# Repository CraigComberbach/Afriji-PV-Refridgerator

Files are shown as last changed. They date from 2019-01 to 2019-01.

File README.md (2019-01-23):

Afriji PV Refridgerator Inverter
================================

Project Details
---------------

* Authors: Craig Comberbach, Mike Mackay
* Processor: PIC24FJ256GA110
* Version Control: This code uses Semantic Versioning (http://semver.org/). The code is setup to auto handle changes to source files it depends upon as long as the associated *.h file has the *_MAJOR, *_MINOR, and _PATCH definitions updated every time the file version changes.

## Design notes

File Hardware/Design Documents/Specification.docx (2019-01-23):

Afriji Spec

Specifications are in black

Details behind specifications are in blue

1. Electrical Ratings
  a. Outputs
    i. 120VAC at 15A initial 0.5 seconds (1800W)
      1. Compressor startup current
    ii. 120VAC at 1A normal operation (120W)
    iii. User LED indicators
      1. Individual Red, Green, Blue
    iv. Console Interface
      1. Outgoing TX only, 3.3V
      2. Used for data logging and debugging during development
  b. Inputs
    i. Vin between a minimum of 9V to a maximum of 37.8V
      1. 3x car batteries @ 12.6V each
    ii. 6x Generic use temperature inputs
      1. 1x for inside of fridge portion
      2. 3x for inside of freezer portion between water shield and freezer interior
      3. 1x for ambient outside air temperature
      4. 1x for ambient enclosure temperature
  c. Longevity
    i. Must last 2000 hours of operation
      1. Not necessarily continuous
      2. We are relying heavily on bulk capacitance which means electrolytic and longer lifespans are hard to come by given the budget
      3. Running for 1 hour a day gives nearly 5.5 years of operation which is an acceptable lifespan

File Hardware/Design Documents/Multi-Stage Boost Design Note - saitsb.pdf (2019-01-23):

1 INTRODUCTION
Devices based on functional material require high voltage for their regular operation e.g. electrostatically actuated MEMS devices, tunable ferroelectric materials [Ning et al. (2014)] etc. all operate on more than 100V. Availability of higher voltage also allows the MEMS chip designers to save the silicon area. For example in MEMS devices comb drives are used for electrostatic actuation. Force generated by the comb drive is directly proportional to the square of applied voltage. This effect enables the designer to reduce the comb size if higher input voltage is available [Khan at al. (2010)]. Analytically saying if a comb drive is designed to generate a certain amount of force at 100V, the same amount of force can be generated by a 16 times smaller comb drive if 400V are applied at its input. This shows that the availability of high voltage can tremendously reduce the size of electrostatic actuators and can help in packing more functionality in the same silicon area.
Supply voltage of digital ICs is continuously reducing. In most of the applications high voltage devices have to be controlled by digital ICs which are mostly operating on either 5V of power supply or 3.3V of battery. To avoid the use of two different voltage sources in a system (one for the digital part and one for the high voltage I/O part) DC-DC converters are required. A number of DC-DC boost converter ICs are available in the market which can provide tens of volts at their output.

LT3494 (2006) is an IC developed by Linear Technology which can perform 3V - 40V conversion. LT3460 (2007) is another IC developed by the same company and is capable of 2.5V 36V conversion and provides better output current as compared to LT3494. Texas Instruments has also developed an IC [TPS61045 (2009)] for DC-DC conversion. Their IC is capable of 1.8V 28V conversion and has the maximum efficiency of 85%. All previously mentioned ICs require off-chip components and their output voltage is less than 50V.
Past research was mainly focused on increasing the efficiency of low voltage DC-DC converters. For example Kong et al. (2012) have improved the efficiency of a 3.7V-8V boost converter. Nakase et al. (2013) have presented a boost system which is capable of 1.03V-5V conversion. Wang et al. (2013) have also represented a 5V-12V boost converter with improved efficiency.
In the last couple of years, research attention has been diverted towards the development of high voltage converters. Jeon et al. (2013) have developed a single stage boost converter which is capable of 3.3V-80V conversion. Shen et al. (2012) have presented a charge pump design which can generate 120V at its output. Test results of this chip are later published by Hofmann et al. (2012). Output of this circuit is not adjustable and the output current is also limited due to the use of charge pump circuit topology.

## Two stage Boost system capable of 5V to 192V-440V DC-DC conversion

### M.B. Saif & K. Hofmann

Integrated Electronic System Lab, Technische Universität Darmstadt, Darmstadt, Hessen, Germany.

ABSTRACT: Numerous electronic and MEMS devices based on functional materials require an ultra-high electrical field and thus a high electrical voltage for their operation, while only a negligible current is needed whereas ubiquitous and mobile computing applications of these devices only support a low voltage source for energy supply. Which often come in the form of a small form factor battery with a typical voltage of 3.7V - 5V. In such scenarios DC-DC conversion becomes essential. In this work a two stage boost system is presented which can provide 192V to 440V at its output while using a 5V input supply. Output can be adjusted by changing the values of inductors from 10µH to 120µH. Converter has been designed and fabricated in 1um SOI process. In the results it is also demonstrated that the two stage boost circuit requires 45.8% less combined inductance as compared to the single stage design.

In none of the previous approaches ultra-high voltage (400V+) conversions were attempted. The highest achieved output voltage is 120V [Shen et al. (2012)]. In this work a two stage boost circuit is represented which is capable of performing ultra- high voltage conversions. By using the 5V input supply the designed converter can generate 192- 440V at the output. Output voltage is adjusted by the varying the value of external inductors from 10µH to 120µH.
The remainder of the paper is organized as follows. In the next section proposed converter topology is discussed. Section 3 elaborates the modified boost circuit architecture. Chip fabrication is presented in Section 4 and results are discussed in Section 5. At the end paper is concluded in Section 6.
2 PROPOSED CONVERTER TOPOLOGY
In this section the design goals and the proposed design is discussed. Design goals can be summarized in following three points
1) System should be capable of doing 5V - 400+ V conversions.
2) Output of the system should be adjustable to widen the application domain.
3) If external components have to be used, their size should be minimal, so that in future they can be monolithically integrated or packaged together with the chip
For high voltage conversion charge pump circuit topology or the boost circuit topology can be used. Charge pumps have the advantage of no off-chip component but their efficiency is compromised due to high number of required stages and in comparison to boost circuits, charge pumps provide less output current. Due to the before mentioned reasons most of the commercially available ICs like LT3494 (2006), TPS61045 (2009), LT3460 (2007) uses the boost circuit.
The output of the charge pump is fixed and to make it adjustable DAC array has to be used as shown by Ning et al. (2014). In contrast to charge pump the output of the boost circuit can be varied by changing the external inductor. This adjustability is the second design goal of this work.
Owing to above mentioned reasons, boost circuit topology was selected. Boost circuits definitely have the disadvantage of external inductors but its output current and efficiency at high voltage conversions make it a better candidate. In order to fulfill the third design goal, 5V- 400+ V conversions should be done by using minimum external inductance. In the next section an endeavor has been made to minimize the required inductance.

3 BOOST CIRCUIT ARCHITECTURE
In this section initially basic operation of the single stage boost circuit is discussed. Later it is improved by using the discontinuous conduction mode (DCM) and two stage architecture.
Schematic of the boost circuit is shown in Figure
1. Its working can be divided into two phases. In charging phase switching stage is closed and the diode is reversed biased. In this circuit configuration inductor charges until a steady state is achieved. The second spike generation phase starts by the opening of switching stage. Opening of switching stage interrupts the inductor current which results in the generation of a voltage spike whose magnitude can be found by using equation 1.
1

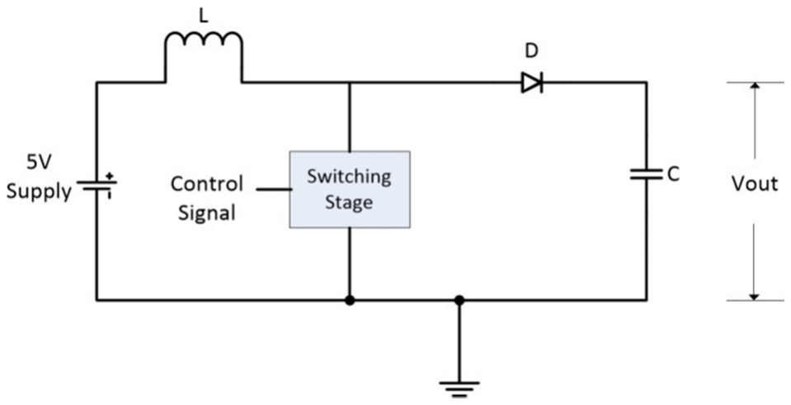
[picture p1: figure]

Figure 1. Single stage Boost circuit
Polarities of the generated voltage spike and the input voltage source add up and momentarily make the diode forward biased which allows the transfer of generated voltage to the capacitor.
From equation (1) it is clear that to increase the generated voltage, either inductance or the rate of change of current has to be changed. Rate of change of inductors current is dependent upon the time required to turn off the high voltage transistors used in the switching stage. Transistors turn off time is the sum of turn off delay, fall time and the reverse recovery time. For the selected technology (xdh10) and transistors the minimum turn-off time is 3.415µs [7].
By using the information of duty cycle and the minimum turn-off time, maximum clock frequency of the boost circuit in continuous conduction mode (CCM) can be determined. In CCM, the duty cycle of the boost circuit can be found by equation (2)
2

For 5V-400V conversion, Vo = 400V and Vs = 5V. By substituting these values in equation (2), the value of required duty cycle is obtained and i.e. D =

98.75%. This implies that turn-off duration for the transistors of switching stage would be only 1.25% time of the clock period. If it is assumed that 1.25% time of the clock period is 3.415 µs (i.e. the minimum turn-off time) then 100% time of the clock period would be
3.415
0.0125 273.2

Maximum operating frequency can be found by taking the inverse of above found time period i.e.

1
273.2

3.66

For a boost circuit the above stated frequency is quite low and if it is used it would result in a very large inductor. Exact value of inductor can be found by using equation (3)
1
2

3

As stated in the introduction the targeted load for this work is the devices which require high voltage but low current. For the sake of calculation, here a load current of 10µA is assumed. At 400V, load current of 10uA results in a load resistance ® of 40

M. By substituting the values of D, R and f in equation
(3) we get the value of minimum required inductor and that is
L 843 mH
In currently available IC technology, fabrication of such a big inductor is not possible. This value should be reduced so that in future at least 3D packaging can be tried. To reduce the inductor size, the boost circuit has to be operated in discontinuous conduction mode (DCM). In DCM the inductor current becomes zero before the start of the next clock cycle. This rapid change in inductor current results in a higher di/dt term. From equation (1) it can be seen that for a fix vL, increase in the rate of change of current results in a reduced value of L. Boost circuit shown in Figure 1 was implemented in cadence ® by using a 1um SOI process (xdh10) from xfab. In post layout simulations it is found that 5V-400V conversion in DCM can be achieved by using a 350µH inductor. To further reduce the inductor size, a multistage approach was analyzed because more inductors connected in series can generate a higher resultant voltage spike. A two stage boost circuit is shown in Figure 2. This concept is also simulated in Cadence ® by using xdh10 technology. The resultant waveform is shown in Figure 4. It can be seen from Figure 4 that with the help of two 120µH external inductor the proposed circuit while operating under discontinuous conduction mode can attain a stable voltage of 435V in just 2ms.
Equivalent circuits of two stage boost when the switches are open and closed are shown in Figure 3. The operation of the circuit can be divided into following two phases.

3.1 Phase 1 (Charging Phase)
When switches are closed, both inductors are in
charging mode. Current | passes
through the inductor L1 and current | passes
through the inductor L2. Maximum value of the charging current is dependent upon the Ron of the switching stages, inductance of the inductor and internal resistance of the inductors.

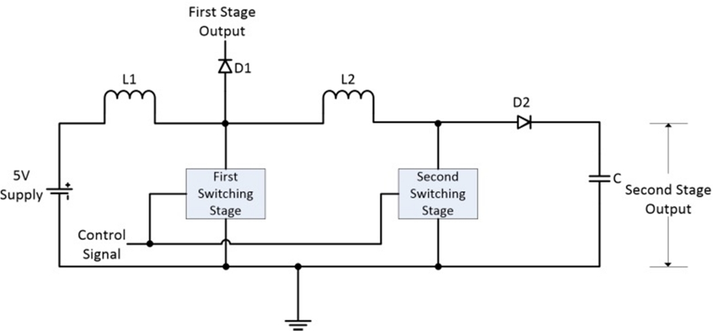
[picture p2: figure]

Figure 2. Two stage Boost Circuit

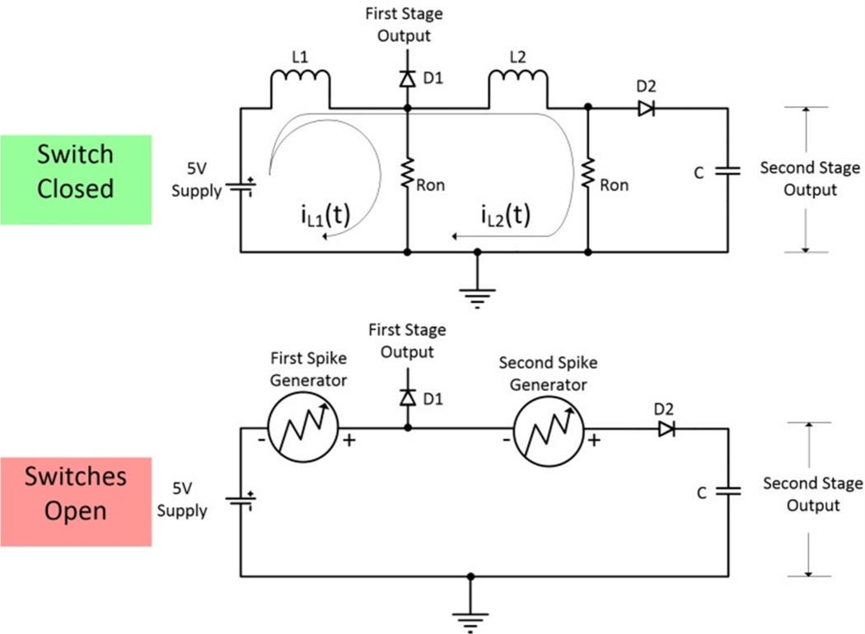
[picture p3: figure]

Figure 3. Equivalent Circuit Topology when switches are close and open

3.2 Phase 2 (Spike Generation)
After the elapse of time DT (D is the duty cycle and T is the time period), switches become open and the normal current flow is interrupted. This interruption in the current flow generates a high voltage spike in both of the inductors and series connection between the inductors adds the generated voltage spikes.

Magnitude of the generated voltage spike can be calculated by using equation (1).
As shown earlier more current passes through L1 in phase 1, which results in a higher voltage spike generated by L1 as compared to L2. Voltage spikes generated by L1 and L2 can be equalized by increasing the inductance of L2.

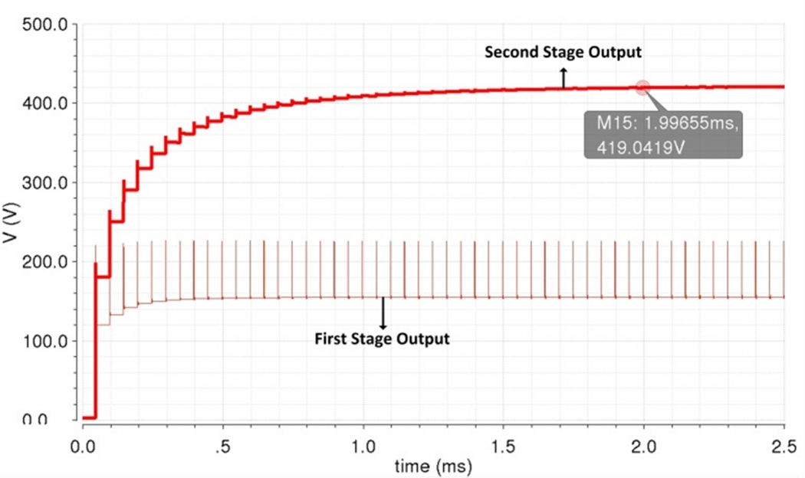
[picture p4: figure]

Figure 4. Transient response of two stage boost converter by using two 120uH inductors
To equalize the voltage spikes L2 L1 and the required value of L2 can be determined by equation (4).

1 4

Inductors of equal inductance can also be used, if the condition formulated in equation (4) is hard to satisfy. In this case the voltages generated by two stages would not be equal.
In the next step designed two stage boost system was simulated in cadence ® with a number of different inductors to ensure the adaptability and stability of the system. It is observed that a number of output voltages can be generated by using different set of inductors.
4 CHIP FABRICATION
To verify the effectiveness of multistage boost architecture a chip has to be designed and fabricated.

As an initial step all the available high voltage IC technologies were analyzed for this specific design and it is found that xdh10 [7] best suits the requirements. Xdh10 is a 1µm SOI process from xfab.
Designed chip includes switching stages, diodes for both stages, and a 265pF capacitor at the output of stage 2. All these components are optimized, to handle the voltage up to 650V. Trenches are placed around the capacitor, diodes and switching stages so that leakage current can be reduced and a problem in one part does not affect the others. Size of the chip is 35 mm² and its picture is shown in Figure 5. Schematic of the chip is shown in Figure 2. Due to the on-chip capacitor for stage 2 its output is automatically low pass filtered. At the output of first stage, voltage spikes are produced (one spike/clock cycle). These spikes can also be converted into a stable voltage by using an external capacitor. Attachment of an external capacitor gives the chip ability to produce two stable output voltages at the same time. Chip output with two 120uH inductor is shown in Figure 6. At the input 5V and the clock signal are supplied externally. Clock current is quite low because it has to only drive the gate terminal of transistors.

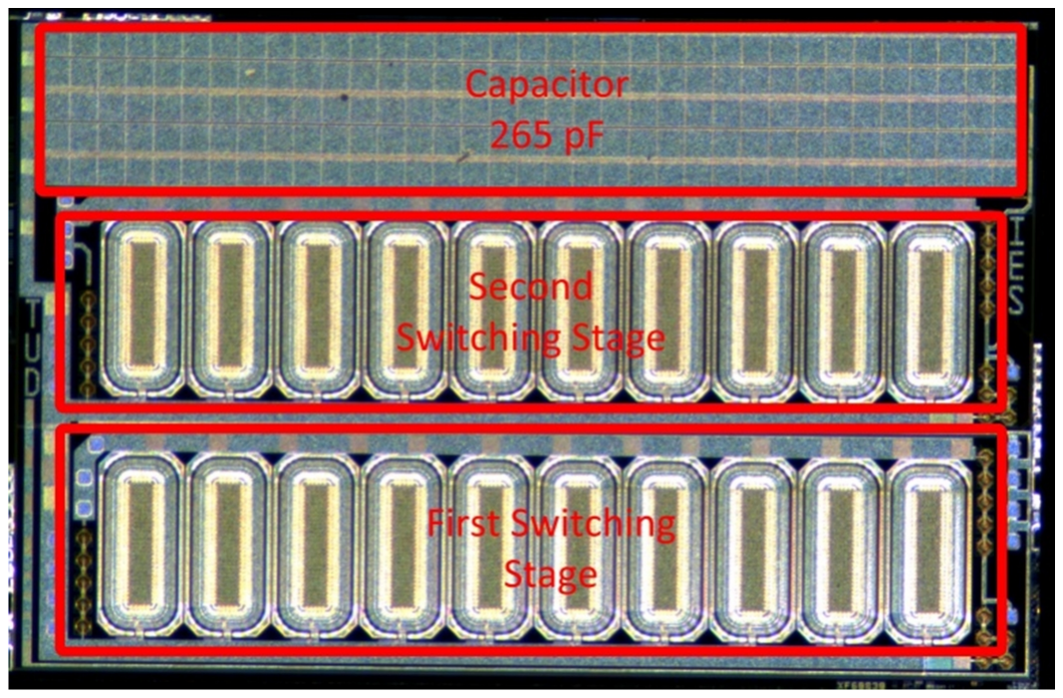
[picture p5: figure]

Figure 5. Picture of fabricated chip

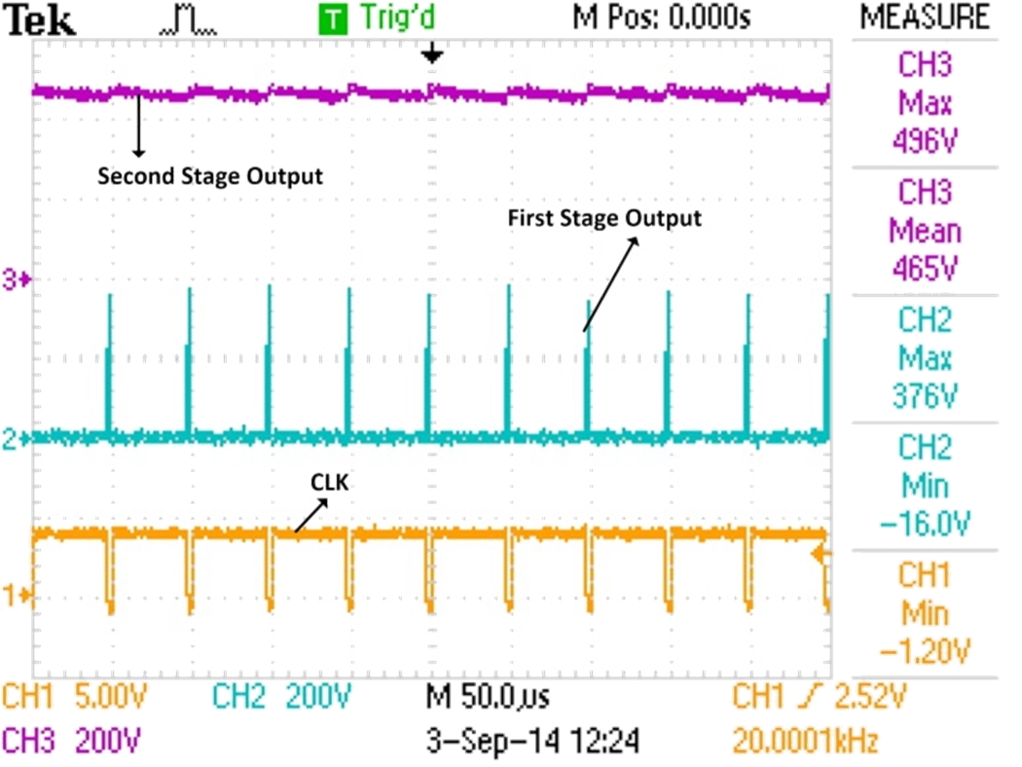
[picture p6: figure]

Figure 6. Chip output when two 120uH inductors are used

5 RESULTS
Figure 6 is showing the output of the designed system when two 120µH inductors are used. As designed, stage 1 is producing the voltage spikes and stage 2 is providing a stable output voltage due to the on-chip capacitor. To verify the adaptability of the output voltage, chip has been tested with a number of external inductors and the results are summarized in Table 1. The test setup is shown in Fig 10.
Figure 7 is showing the Vout vs load current graph. It can be seen that an increase in the load current reduces the output voltage. 100µH and 120µH inductors show better voltage stability whereas worst voltage stability is shown by 10µH inductor. System is designed to provide more than10µA at 400V. It can be seen from zoomed voltage curve of 120µH inductors that actual chip can maintain output voltage higher than 400V while supplying more than 70µA load current.
Operating frequency vs load current graph is shown in Figure 8 and it can be seen there that higher load currents require higher operating frequency. Figure 8 is also showing that larger inductors can operate on lower frequencies whereas smaller inductors require higher operating frequencies. Quantitatively speaking 100µH and 120µH inductors can be operated with less than 100 kHz operating frequency for most of the loading conditions whereas smaller inductors (10µH and 15µH) require higher operating frequency in range of 125 kHz to 200 kHz. Higher frequency increases the losses and reduces the efficiency.
Figure 9 is showing the efficiency vs load current graph. Efficiency increases by increasing the load current but at the cost of output voltage. More than 20% efficiency is shown by 47µH, 100µH and 120µH inductors. Best efficiency (i.e. 34.12%) is shown by 100µH inductor at 2.2mA load current. To compare the efficiency with other high voltage converters, charge pump represented by Shen et al. (2012) is considered here. Their charge pump can provide output voltage of 120V, can supply load current up to 100µA and shows 12% efficiency. The boost system presented in this work when operated with 100µH inductors gives 120V output, while supplying a load current of 1mA-2mA and the efficiency of the system varies from 20-34% (higher load current results in better efficiency). When compared at the output voltage of 120V the boost system presented here surely shows better attributes. At higher voltages (400+V) the efficiency is less due to discontinue conduction mode.
The chip is specifically designed to generate 400+V. Such high voltage can be achieved by using either 100µH or 120µH inductors. Due to this design objective chip shows better stability, better efficiency and better load current when operated with 100µH or 120µH inductors.
Smaller inductors (22µH, 15µH and 10µH) can be used if a voltage less than 260V along with lower output current is required. If output voltage is required in the range of 100-250V with a load current of 1-2mA, then the use of 100µH and 120µH inductors is recommended.
From Figure 9 it can be seen that these lower inductors require higher operating frequencies which results in more switching loses and reduced system efficiency.

Table 1: Output voltage at different inductor values
Sr. No. | Inductor | Vout (V)
1 | 2 x 10µH | 192
2 | 2 x 15µH | 260
3 | 2 x 22µH | 250
4 | 2 x 47µH | 350
5 | 2 x 100µH | 408
6 | 2 x 120µH | 440
Chip temperature has also been analyzed during the working of chip. It is found that normally temperature stays between 40o
| | -50oC and
under any loading condition temperature never exceeds 60oC.

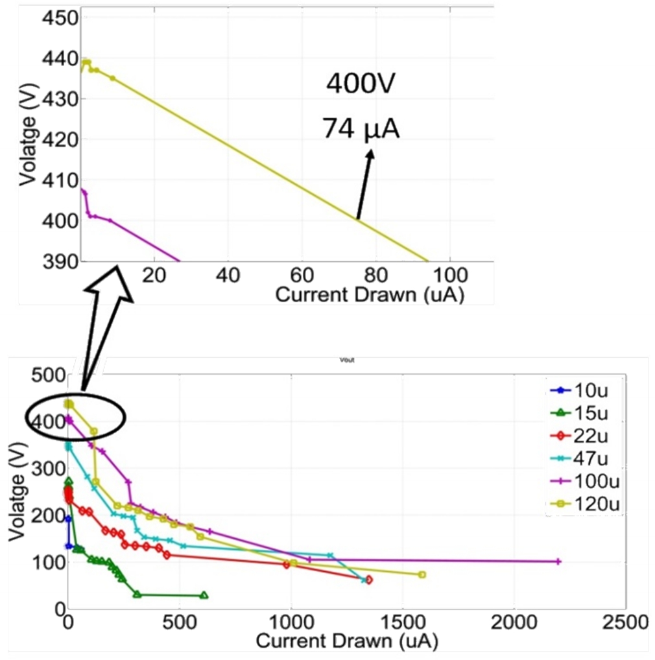
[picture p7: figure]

Figure 7. Output voltage Vs Load current

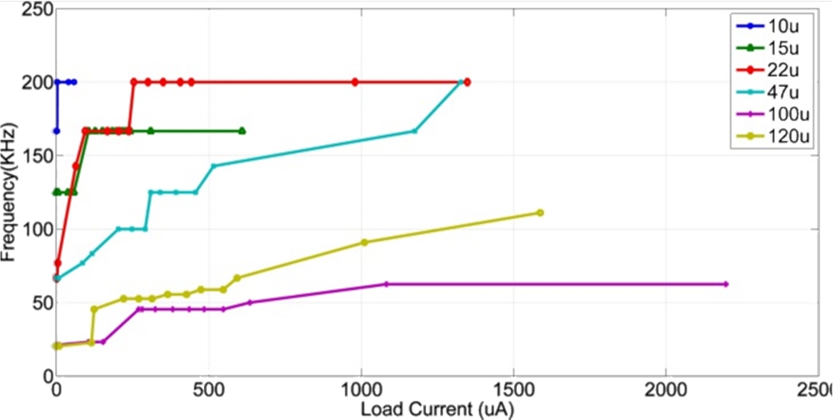
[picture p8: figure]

Figure 8. Frequency vs load current

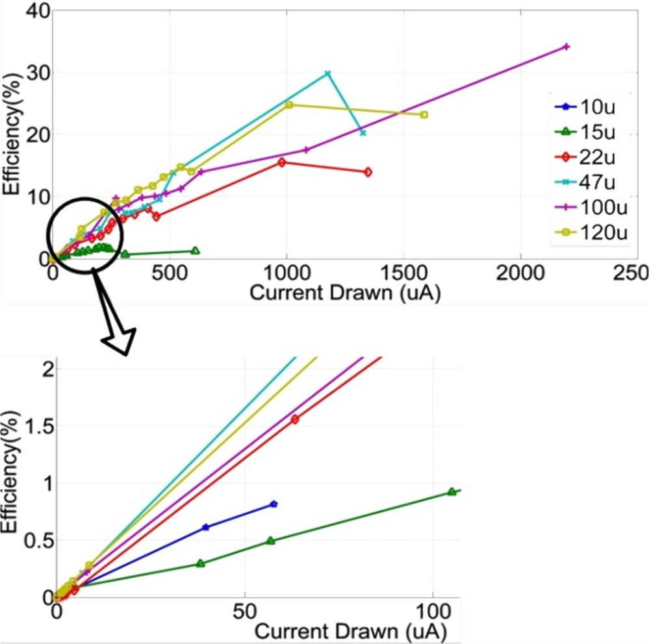
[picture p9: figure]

Figure 9. Efficiency Vs Load current

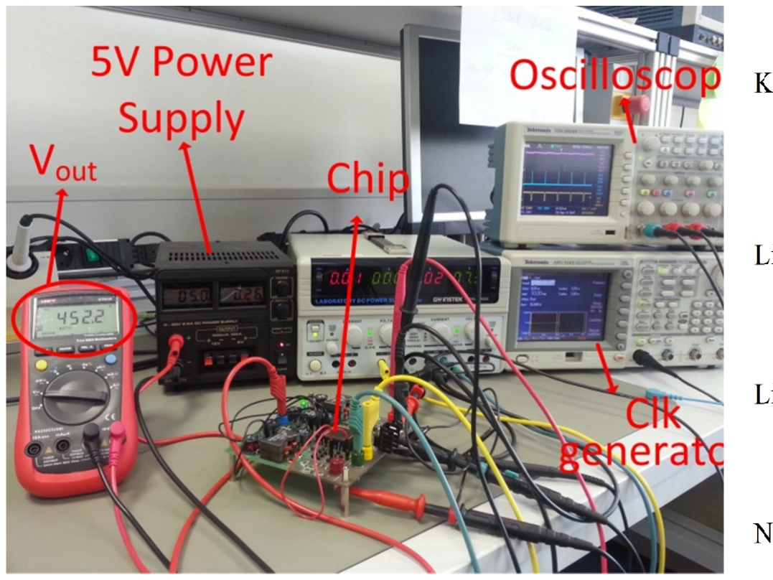
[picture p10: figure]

Figure 10. Test Setup
6 CONCLUSION AND FUTURE WORK
A DC-DC boost converter is presented with a novel two stage architecture. As compared to single stage design, combined inductance (L1 + L2) required by two stage boost converter is 45.8% less. In a single stage design, a single inductor has to bear the full strength of generated voltage spike whereas in two stage architecture the generated voltage spike is divided among the two inductors. This phenomenon reduces the voltage stress on inductors and improves their reliability. If an external capacitor is used with stage 1, two stable output voltages can be attained simultaneously. The presented system can operate with a number of inductors and can produce the output voltages varying from 192V-440V. Inductors can be selected according to the loading conditions.
Output characteristics of the chip are better if larger inductors are used. These inductors also allow the converter to operate on lower frequency, which in turn reduces the switching loses and improves the efficiency.
In future, authors want to further improve the efficiency.

REFERENCES

Hofmann Klaus, Shen Lufei, González- Rodríguez Erick, Maune Holger. 2012. Fully Integrated High Voltage Charge Pump for Energy-efficient Reconfigurable Multi-band RF Transceivers. Telecommunications Energy Conference (INTELEC), IEEE, Sept. 30 - Oct. 4 2012: 1-4.
Jeon Inho, Nam Hyunseok, Lee Heeyoung, Ahn Youngkook, Roh Jeongjin. 2013. An 80-V integrated boost converter for piezoelectric actuators in smartphones. Analog Integrated Circuits and Signal Processing Volume 75, Issue 3, March 2013: 531-537. Khan Fahimullah, Bazaz Shafaat A., Sohail Muhammad. 2010.

Design, implementation and testing of electrostatic SOI MUMPs based microgripper. Journal of Microsystem Technologies, November 2010, Volume 16, Issue 11: 1957- 1965. Kong Tae-Hwang, Hong Sung-Wan, Lee Sungwoo, Im Jong- Pil, Cho Gyu-Hyeong. 2012. A 0.791mm² Fully On-Chip

Controller with Self-Error-Correction for Boost DC-DC Converter Based on Zero-Order Control. Custom Integrated Circuits Conference (CICC), IEEE, 9-12 Sept. 2012: 1-4.
Linear | Technology. | 2007. | LT3460 | Data | sheet,
1.3MHz/650kHz Step-Up DC-DC Converter in SC70, ThinSOT and DFN, 2007, Accessed Dec. 2013, http://cds.linear.com/docs/en/datasheet/34601fb.pdf Linear Technology. 2006. LT3494/LT3494A Data sheet, Micropower Low Noise Boost Converters with Output Disconnect, Nov. 2006, Accessed Dec. 2013, http://cds.linear.com/docs/en/datasheet/3494fb.pdf
Nakase Yasunobu, Hirose Shinichi, Onoda Hiroshi, Ido Yasuhiro, Shimizu Yoshiaki, Oishi Tsukasa, Kumamoto Toshio and Shimizu Toru. 2013. 0.5 V Start-Up 87% Efficiency 0.75 mm² On-Chip Feed-Forward Single-Inductor Dual-Output (SIDO) Boost DC-DC Converter for Battery and Solar Cell Operation Sensor Network Micro- Computer Integration. IEEE Journal of solid-state circuits, vol. 48, no. 8, August 2013:1933-1942. Ning Jing, Shen Lufei, González-Rodríguez Erick, Hofmann

Klaus. 2014. An integrated high voltage digital-to-analog converter for a reconfigurable antenna array, Analog Integrated Circuits and Signal Processing, Volume 80, Issue 3: 407-415.

Shen Lufei, Hofmann Klaus. 2012. Fully Integratable 4-Phase Charge Pump Architecture for High Voltage Applications. 19th International Conference on Mixed Design of Integrated Circuits and Systems, Warsaw (IEEE): 265 268.
Texas Instruments. 2009. TPS61045 Data sheet Rev. B, Digitally Adjustable Boost Converter, Mar. 2009,
Accessed | Dec. | 2013.
http://www.ti.com/lit/ds/symlink/tps61045.pdf
Wang Chen-Yu, Guo Jhih-Sian, Huang Chi-Yuan and Tsai Chien-Hung. 2013. A High Effieciency DC/DC Boost Regulator with Adaptive Off/On-Time Control. International Symposium on VLSI Design, Automation, and Test (VLSI-DAT), IEEE, 22-24 April 2013: 1-4. X-FAB Silicon Foundries, 1.0 Micron Modular 650V Trench Insulated BCD Process Technology (xdh10), Accessed Dec. 2014. http://www.xfab.com/technology/soi/10-um- xdh10/

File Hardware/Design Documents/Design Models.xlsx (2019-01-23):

Don't use this one |  | Thermistor on top
 | Vcc | 3.3
 | Rta (High Temp) | 2000
 | Rtb (Low Temp) | 4500
 | Rb | 2000
 | Rf | 6336.308
 | Vref | 1.425091
Use this one |  | Thermistor on bottom
 | Vcc | 3.3
 | Rt | 2000
 | Rba (Low Temp) | 4500 | 53.5
 | Rbb (High Temp) | 2000 | 76.4
 | Vref Rb | 2000
 | Vref Rt | 1520.171299
 | Rf | 6336.308338
 | Vref | 1.875
188500 | -40
144300 | -35
111300 | -30
86560 | -25
67790 | -20
53460 | -15
42450 | -10
33930 | -5
27280 | 0
22070 | 5
17960 | 10
14700 | 15
12090 | 20
10000 | 25
8312 | 30
6942 | 35
5826 | 40
4911 | 45
4158 | 50
3536 | 55
3019 | 60
2588 | 65
2227 | 70
1924 | 75
1668 | 80
1451 | 85
1267 | 90
1110 | 95
975 | 100
860 | 105
760 | 110
674 | 115
599 | 120
534 | 125

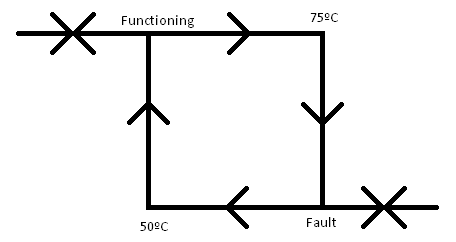
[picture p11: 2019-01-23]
Hardware/Design Documents/Hysterysis.png

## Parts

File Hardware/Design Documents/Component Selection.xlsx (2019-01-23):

Digi-Key Part Number | Description | Quantity Available | Unit Price (CAD) | Capacitance | Voltage - Rated | ESR (Equivalent Series Resistance) | Lifetime @ Temp. | Operating Temperature | Capacitance (mF) | Voltage | F/$
565-2700-ND | CAP ALUM 12000UF 20% 63V SNAP | 926 | 4.15877 | 12000µF | 63V | 21 mOhm @ 120Hz | 2000 Hrs @ 85°C | -40°C ~ 85°C | 12 | 63 | 2.88546854
338-1569-ND | CAP ALUM 10000UF 20% 63V SNAP | 18144 | 3.48091 | 10000µF | 63V | 40 mOhm | 3000 Hrs @ 85°C | -40°C ~ 85°C | 10 | 63 | 2.872811995
338-1570-ND | CAP ALUM 10000UF 20% 63V SNAP | 7934 | 3.60916 | 10000µF | 63V | 40 mOhm | 3000 Hrs @ 85°C | -40°C ~ 85°C | 10 | 63 | 2.770727815
565-4208-ND | CAP ALUM 15000UF 20% 63V SNAP | 194 | 5.42129 | 15000µF | 63V | 14 mOhm @ 120Hz | 2000 Hrs @ 105°C | -40°C ~ 105°C | 15 | 63 | 2.76686914 | 1st Choice input Cap
495-6162-ND | CAP ALUM 6800UF 20% 63V SNAP | 158 | 2.54443 | 6800µF | 63V | - | 2000 Hrs @ 85°C | -40°C ~ 85°C | 6.8 | 63 | 2.672504254
338-3908-ND | CAP ALUM 15000UF 20% 63V SNAP | 663 | 5.62207 | 15000µF | 63V | 24 mOhm @ 120Hz | 3000 Hrs @ 105°C | -40°C ~ 105°C | 15 | 63 | 2.668056428 | 2nd Choice input Cap
338-4413-ND | CAP ALUM 6800UF 20% 63V SNAP | 1000 | 2.56841 | 6800µF | 63V | 59 mOhm @ 120Hz | 3000 Hrs @ 85°C | -40°C ~ 85°C | 6.8 | 63 | 2.647552377
493-6137-ND | CAP ALUM 10000UF 20% 63V SNAP | 1321 | 3.86565 | 10000µF | 63V | - | 3000 Hrs @ 105°C | -40°C ~ 105°C | 10 | 63 | 2.586887069
565-2698-ND | CAP ALUM 10000UF 20% 63V SNAP | 1241 | 3.90229 | 10000µF | 63V | 25 mOhm @ 120Hz | 2000 Hrs @ 85°C | -40°C ~ 85°C | 10 | 63 | 2.562597859
338-1663-ND | CAP ALUM 8200UF 20% 63V SNAP | 685 | 3.2061 | 8200µF | 63V | 49 mOhm | 3000 Hrs @ 85°C | -40°C ~ 85°C | 8.2 | 63 | 2.557624528
495-6154-ND | CAP ALUM 3900UF 20% 63V SNAP | 140 | 1.54939 | 3900µF | 63V | - | 2000 Hrs @ 85°C | -40°C ~ 85°C | 3.9 | 63 | 2.517119641
338-1651-ND | CAP ALUM 6800UF 20% 63V SNAP | 1289 | 2.70158 | 6800µF | 63V | 59 mOhm | 3000 Hrs @ 85°C | -40°C ~ 85°C | 6.8 | 63 | 2.517045581
1572-1070-ND | SNAP MOUNT 85C | 1395 | 4.03786 | 10000µF | 63V | 24.87 mOhm @ 120Hz | 3000 Hrs @ 85°C | -40°C ~ 85°C | 10 | 63 | 2.476559366
495-6152-ND | CAP ALUM 12000UF 20% 63V SNAP | 35 | 4.85451 | 12000µF | 63V | - | 2000 Hrs @ 85°C | -40°C ~ 85°C | 12 | 63 | 2.471928166
565-2699-ND | CAP ALUM 10000UF 20% 63V SNAP | 198 | 4.06717 | 10000µF | 63V | 25 mOhm @ 120Hz | 2000 Hrs @ 85°C | -40°C ~ 85°C | 10 | 63 | 2.458712077
338-1652-ND | CAP ALUM 6800UF 20% 63V SNAP | 223 | 2.81573 | 6800µF | 63V | 59 mOhm | 3000 Hrs @ 85°C | -40°C ~ 85°C | 6.8 | 63 | 2.41500428
493-7179-ND | CAP ALUM 6800UF 20% 63V SNAP | 828 | 2.82137 | 6800µF | 63V | - | 3000 Hrs @ 105°C | -40°C ~ 105°C | 6.8 | 63 | 2.410176616
565-2918-ND | CAP ALUM 10000UF 20% 63V SNAP | 753 | 4.15877 | 10000µF | 63V | 25 mOhm @ 120Hz | 2000 Hrs @ 105°C | -40°C ~ 105°C | 10 | 63 | 2.404557117
495-6169-ND | CAP ALUM 4700UF 20% 63V SNAP | 233 | 1.95998 | 4700µF | 63V | - | 2000 Hrs @ 85°C | -40°C ~ 85°C | 4.7 | 63 | 2.397983653
338-2104-ND | CAP ALUM 22000UF 20% 63V SNAP | 113 | 9.1815 | 22000µF | 63V | - | 3000 Hrs @ 85°C | -40°C ~ 85°C | 22 | 63 | 2.396122638
565-2697-ND | CAP ALUM 8200UF 20% 63V SNAP | 107 | 3.46259 | 8200µF | 63V | 30 mOhm @ 120Hz | 2000 Hrs @ 85°C | -40°C ~ 85°C | 8.2 | 63 | 2.368169492
338-3812-ND | CAP ALUM 18000UF 20% 63V SNAP | 2501 | 7.6117 | 18000µF | 63V | 23 mOhm @ 120Hz | 3000 Hrs @ 85°C | -40°C ~ 85°C | 18 | 63 | 2.364780535
565-2695-ND | CAP ALUM 6800UF 20% 63V SNAP | 683 | 2.87633 | 6800µF | 63V | 37 mOhm @ 120Hz | 2000 Hrs @ 85°C | -40°C ~ 85°C | 6.8 | 63 | 2.364123727
338-2102-ND | CAP ALUM 18000UF 20% 63V SNAP | 560 | 7.68472 | 18000µF | 63V | - | 3000 Hrs @ 85°C | -40°C ~ 85°C | 18 | 63 | 2.342310455
1572-1326-ND | CAP ALUM 10000UF 20% 63V SNAP | 60 | 4.36397 | 10000µF | 63V | 49.74 mOhm @ 120Hz | 2000 Hrs @ 85°C | -40°C ~ 85°C | 10 | 63 | 2.291491463
338-2721-ND | CAP ALUM 12000UF 20% 63V SNAP | 33 | 5.23875 | 12000µF | 63V | - | 3000 Hrs @ 105°C | -40°C ~ 105°C | 12 | 63 | 2.290622763
338-1629-ND | CAP ALUM 4700UF 20% 63V SNAP | 9 | 2.07376 | 4700µF | 63V | 85 mOhm | 3000 Hrs @ 85°C | -40°C ~ 85°C | 4.7 | 63 | 2.266414629
493-1133-ND | CAP ALUM 4700UF 20% 63V RADIAL | 1587 | 2.07984 | 4700µF | 63V | - | 2000 Hrs @ 85°C | -40°C ~ 85°C | 4.7 | 63 | 2.259789215
1189-2901-ND | CAP ALUM 10000UF 20% 63V SNAP | 288 | 4.43157 | 10000µF | 63V | - | 2000 Hrs @ 105°C | -40°C ~ 105°C | 10 | 63 | 2.256536622
493-12479-ND | CAP ALUM 6800UF 20% 63V RADIAL | 183 | 3.05221 | 6800µF | 63V | - | 1000 Hrs @ 105°C | -55°C ~ 105°C | 6.8 | 63 | 2.227893887
565-2696-ND | CAP ALUM 6800UF 20% 63V SNAP | 427 | 3.05954 | 6800µF | 63V | 37 mOhm @ 120Hz | 2000 Hrs @ 85°C | -40°C ~ 85°C | 6.8 | 63 | 2.222556332
493-7281-ND | CAP ALUM 12000UF 20% 63V SNAP | 185 | 5.42074 | 12000µF | 63V | - | 3000 Hrs @ 85°C | -40°C ~ 85°C | 12 | 63 | 2.213719898
338-2719-ND | CAP ALUM 10000UF 63V 20% SNAP | 1006 | 4.56183 | 10000µF | 63V | - | 3000 Hrs @ 105°C | -40°C ~ 105°C | 10 | 63 | 2.192102731
565-2917-ND | CAP ALUM 8200UF 20% 63V SNAP | 825 | 3.75572 | 8200µF | 63V | 30 mOhm @ 120Hz | 2000 Hrs @ 105°C | -40°C ~ 105°C | 8.2 | 63 | 2.183336351
493-7280-ND | CAP ALUM 10000UF 20% 63V SNAP | 1 | 4.59221 | 10000µF | 63V | - | 3000 Hrs @ 85°C | -40°C ~ 85°C | 10 | 63 | 2.177600763
1572-1501-ND | CAP ALUM 4700UF 20% 63V SNAP | 45 | 2.17649 | 4700µF | 63V | 105.82 mOhm @ 120Hz | 2000 Hrs @ 85°C | -40°C ~ 85°C | 4.7 | 63 | 2.1594402
399-6531-ND | CAP ALUM 12000UF 20% 63V SNAP | 334 | 5.56092 | 12000µF | 63V | - | 2000 Hrs @ 85°C | -40°C ~ 85°C | 12 | 63 | 2.157916316
493-7293-ND | CAP ALUM 6800UF 20% 63V SNAP | 160 | 3.17001 | 6800µF | 63V | - | 3000 Hrs @ 85°C | -40°C ~ 85°C | 6.8 | 63 | 2.145103643
493-1130-ND | CAP ALUM 2200UF 20% 63V RADIAL | 1296 | 1.03325 | 2200µF | 63V | - | 2000 Hrs @ 85°C | -40°C ~ 85°C | 2.2 | 63 | 2.129203968
493-7295-ND | CAP ALUM 8200UF 20% 63V SNAP | 66 | 3.88011 | 8200µF | 63V | - | 3000 Hrs @ 85°C | -40°C ~ 85°C | 8.2 | 63 | 2.113342148
565-2691-ND | CAP ALUM 4700UF 20% 63V SNAP | 177 | 2.22596 | 4700µF | 63V | 53 mOhm @ 120Hz | 2000 Hrs @ 85°C | -40°C ~ 85°C | 4.7 | 63 | 2.111448544
493-13920-ND | CAP ALUM 6800UF 20% 80V SNAP | 68 | 3.22442 | 6800µF | 80V | - | 3000 Hrs @ 85°C | -40°C ~ 85°C | 6.8 | 80 | 2.108906408
495-6153-ND | CAP ALUM 2200UF 20% 63V SNAP | 340 | 1.04449 | 2200µF | 63V | - | 2000 Hrs @ 85°C | -40°C ~ 85°C | 2.2 | 63 | 2.106291109
493-7176-ND | CAP ALUM 4700UF 20% 63V SNAP | 651 | 2.24498 | 4700µF | 63V | - | 3000 Hrs @ 105°C | -40°C ~ 105°C | 4.7 | 63 | 2.093559854
565-2693-ND | CAP ALUM 5600UF 20% 63V SNAP | 71 | 2.68256 | 5600µF | 63V | 44 mOhm @ 120Hz | 2000 Hrs @ 85°C | -40°C ~ 85°C | 5.6 | 63 | 2.087558153
493-13922-ND | CAP ALUM 8200UF 20% 80V SNAP | 124 | 3.95725 | 8200µF | 80V | - | 3000 Hrs @ 85°C | -40°C ~ 85°C | 8.2 | 80 | 2.072146061
1572-1081-ND | SNAP MOUNT 85C | 108 | 7.26489 | 15000µF | 63V | 16.58 mOhm @ 120Hz | 3000 Hrs @ 85°C | -40°C ~ 85°C | 15 | 63 | 2.064724999
P5198-ND | CAP ALUM 2200UF 20% 63V RADIAL | 1080 | 1.067 | 2200µF | 63V | - | 2000 Hrs @ 85°C | -40°C ~ 85°C | 2.2 | 63 | 2.06185567
493-7294-ND | CAP ALUM 6800UF 20% 63V SNAP | 194 | 3.30101 | 6800µF | 63V | - | 3000 Hrs @ 85°C | -40°C ~ 85°C | 6.8 | 63 | 2.059975583
565-2689-ND | CAP ALUM 3900UF 20% 63V SNAP | 460 | 1.92156 | 3900µF | 63V | 64 mOhm @ 120Hz | 2000 Hrs @ 85°C | -40°C ~ 85°C | 3.9 | 63 | 2.029600949
493-7292-ND | CAP ALUM 5600UF 20% 63V SNAP | 39 | 2.77666 | 5600µF | 63V | - | 3000 Hrs @ 85°C | -40°C ~ 85°C | 5.6 | 63 | 2.016811565
1189-2867-ND | CAP ALUM 6800UF 20% 63V SNAP | 69 | 3.37429 | 6800µF | 63V | - | 2000 Hrs @ 105°C | -40°C ~ 105°C | 6.8 | 63 | 2.015238761
565-2916-ND | CAP ALUM 6800UF 20% 63V SNAP | 871 | 3.40763 | 6800µF | 63V | 37 mOhm @ 120Hz | 2000 Hrs @ 105°C | -40°C ~ 105°C | 6.8 | 63 | 1.995521814
493-8447-ND | CAP ALUM 5600UF 20% 63V SNAP | 4 | 2.81573 | 5600µF | 63V | - | 3000 Hrs @ 105°C | -40°C ~ 105°C | 5.6 | 63 | 1.988827054
493-7291-ND | CAP ALUM 5600UF 20% 63V SNAP | 1086 | 2.8203 | 5600µF | 63V | - | 3000 Hrs @ 85°C | -40°C ~ 85°C | 5.6 | 63 | 1.985604368
493-12414-ND | CAP ALUM 6800UF 20% 63V RADIAL | 123 | 3.43859 | 6800µF | 63V | - | 2000 Hrs @ 85°C | -40°C ~ 85°C | 6.8 | 63 | 1.977554754
565-2694-ND | CAP ALUM 5600UF 20% 63V SNAP | 153 | 2.83477 | 5600µF | 63V | 44 mOhm @ 120Hz | 2000 Hrs @ 85°C | -40°C ~ 85°C | 5.6 | 63 | 1.975468909
338-2323-ND | CAP ALUM 6800UF 63V 20% SNAP | 1269 | 3.44427 | 6800µF | 63V | - | 3000 Hrs @ 105°C | -40°C ~ 105°C | 6.8 | 63 | 1.974293537
493-7178-ND | CAP ALUM 5600UF 20% 63V SNAP | 118 | 2.85875 | 5600µF | 63V | - | 3000 Hrs @ 105°C | -40°C ~ 105°C | 5.6 | 63 | 1.95889812
338-1458-ND | CAP ALUM 10000UF 20% 63V SNAP | 1330 | 5.14748 | 10000µF | 63V | 40 mOhm | 3000 Hrs @ 105°C | -40°C ~ 105°C | 10 | 63 | 1.942698175
493-13921-ND | CAP ALUM 6800UF 20% 80V SNAP | 182 | 3.51755 | 6800µF | 80V | - | 3000 Hrs @ 85°C | -40°C ~ 85°C | 6.8 | 80 | 1.933163708
1189-2902-ND | CAP ALUM 8200UF 20% 63V SNAP | 58 | 4.24195 | 8200µF | 63V | - | 2000 Hrs @ 105°C | -40°C ~ 105°C | 8.2 | 63 | 1.933073233
338-1987-ND | CAP ALUM 39000UF 20% 80V SNAP | 25 | 20.26258 | 39000µF | 80V | - | 3000 Hrs @ 85°C | -40°C ~ 85°C | 39 | 80 | 1.924730217
493-13918-ND | CAP ALUM 5600UF 20% 80V SNAP | 28 | 2.91297 | 5600µF | 80V | - | 3000 Hrs @ 85°C | -40°C ~ 85°C | 5.6 | 80 | 1.922436551
493-7174-ND | CAP ALUM 3900UF 20% 63V SNAP | 15 | 2.05473 | 3900µF | 63V | - | 3000 Hrs @ 105°C | -40°C ~ 105°C | 3.9 | 63 | 1.898059599
338-2687-ND | CAP ALUM 12000UF 20% 63V SNAP | 1436 | 6.33396 | 12000µF | 63V | 28 mOhm @ 120Hz | 3000 Hrs @ 85°C | -40°C ~ 85°C | 12 | 63 | 1.894549381
493-12411-ND | CAP ALUM 2200UF 20% 63V RADIAL | 168 | 1.16524 | 2200µF | 63V | - | 2000 Hrs @ 85°C | -40°C ~ 85°C | 2.2 | 63 | 1.888023068
493-12413-ND | CAP ALUM 4700UF 20% 63V RADIAL | 250 | 2.51038 | 4700µF | 63V | - | 2000 Hrs @ 85°C | -40°C ~ 85°C | 4.7 | 63 | 1.872226516
493-6162-ND | CAP ALUM 4700UF 20% 80V SNAP | 541 | 2.51133 | 4700µF | 80V | - | 3000 Hrs @ 85°C | -40°C ~ 85°C | 4.7 | 80 | 1.871518279
493-1129-ND | CAP ALUM 1000UF 20% 63V RADIAL | 17792 | 0.53461 | 1000µF | 63V | - | 2000 Hrs @ 85°C | -40°C ~ 85°C | 1 | 63 | 1.870522437
493-7289-ND | CAP ALUM 4700UF 20% 63V SNAP | 8 | 2.51342 | 4700µF | 63V | - | 3000 Hrs @ 85°C | -40°C ~ 85°C | 4.7 | 63 | 1.869962044
338-2024-ND | CAP ALUM 12000UF 20% 63V SNAP | 672 | 6.44348 | 12000µF | 63V | - | 3000 Hrs @ 105°C | -40°C ~ 105°C | 12 | 63 | 1.862347675
1189-2866-ND | CAP ALUM 4700UF 20% 63V SNAP | 180 | 2.52732 | 4700µF | 63V | - | 2000 Hrs @ 105°C | -40°C ~ 105°C | 4.7 | 63 | 1.859677445
338-1589-ND | CAP ALUM 2200UF 20% 63V SNAP | 598 | 1.18379 | 2200µF | 63V | 181 mOhm | 3000 Hrs @ 85°C | -40°C ~ 85°C | 2.2 | 63 | 1.85843773
1572-1055-ND | CAP ALUM 1000UF 20% 63V RADIAL | 1523 | 0.53905 | 1000µF | 63V | 149.2 mOhm @ 120Hz | 2000 Hrs @ 105°C | -40°C ~ 105°C | 1 | 63 | 1.855115481
493-11027-ND | CAP ALUM 2200UF 20% 63V RADIAL | 308 | 1.18774 | 2200µF | 63V | - | 2000 Hrs @ 85°C | -40°C ~ 85°C | 2.2 | 63 | 1.852257228
338-2275-ND | CAP ALUM 8200UF 20% 80V SNAP | 211 | 4.43358 | 8200µF | 80V | 40 mOhm @ 120Hz | 3000 Hrs @ 85°C | -40°C ~ 85°C | 8.2 | 80 | 1.849521154
P5197-ND | CAP ALUM 1000UF 20% 63V RADIAL | 2841 | 0.54307 | 1000µF | 63V | - | 2000 Hrs @ 85°C | -40°C ~ 85°C | 1 | 63 | 1.841383247
338-2025-ND | CAP ALUM 15000UF 20% 63V SNAP | 936 | 8.15931 | 15000µF | 63V | - | 3000 Hrs @ 105°C | -40°C ~ 105°C | 15 | 63 | 1.838390746
493-11033-ND | CAP ALUM 4700UF 20% 63V RADIAL | 240 | 2.56537 | 4700µF | 63V | - | 2000 Hrs @ 85°C | -40°C ~ 85°C | 4.7 | 63 | 1.832094396
493-13919-ND | CAP ALUM 5600UF 20% 80V SNAP | 1010 | 3.05954 | 5600µF | 80V | - | 3000 Hrs @ 85°C | -40°C ~ 85°C | 5.6 | 80 | 1.830340509
493-8446-ND | CAP ALUM 4700UF 20% 63V SNAP | 3047 | 2.56841 | 4700µF | 63V | - | 3000 Hrs @ 105°C | -40°C ~ 105°C | 4.7 | 63 | 1.829925907
565-2912-ND | CAP ALUM 4700UF 20% 63V SNAP | 599 | 2.56841 | 4700µF | 63V | 53 mOhm @ 120Hz | 2000 Hrs @ 105°C | -40°C ~ 105°C | 4.7 | 63 | 1.829925907
338-2568-ND | CAP ALUM 6800UF 20% 63V SNAP | 2173 | 3.71908 | 6800µF | 63V | - | 3000 Hrs @ 105°C | -40°C ~ 105°C | 6.8 | 63 | 1.828409176
338-2101-ND | CAP ALUM 12000UF 20% 63V SNAP | 113 | 6.57126 | 12000µF | 63V | - | 3000 Hrs @ 85°C | -40°C ~ 85°C | 12 | 63 | 1.826133801
565-2688-ND | CAP ALUM 3300UF 20% 63V SNAP | 225 | 1.8112 | 3300µF | 63V | 75 mOhm @ 120Hz | 2000 Hrs @ 85°C | -40°C ~ 85°C | 3.3 | 63 | 1.821996466
565-2914-ND | CAP ALUM 5600UF 20% 63V SNAP | 390 | 3.07786 | 5600µF | 63V | 44 mOhm @ 120Hz | 2000 Hrs @ 105°C | -40°C ~ 105°C | 5.6 | 63 | 1.819445979
493-1363-ND | CAP ALUM 6800UF 20% 63V RADIAL | 820 | 3.73776 | 6800µF | 63V | - | 1000 Hrs @ 105°C | -55°C ~ 105°C | 6.8 | 63 | 1.819271435
338-1986-ND | CAP ALUM 33000UF 20% 80V SNAP | 35 | 18.21856 | 33000µF | 80V | - | 3000 Hrs @ 85°C | -40°C ~ 85°C | 33 | 80 | 1.811339645
338-1542-ND | CAP ALUM 6800UF 20% 63V SNAP | 379 | 3.79236 | 6800µF | 63V | 59 mOhm | 3000 Hrs @ 105°C | -40°C ~ 105°C | 6.8 | 63 | 1.793078716
338-2027-ND | CAP ALUM 18000UF 20% 63V SNAP | 146 | 10.07592 | 18000µF | 63V | - | 3000 Hrs @ 105°C | -40°C ~ 105°C | 18 | 63 | 1.786437368
493-11034-ND | CAP ALUM 6800UF 20% 63V RADIAL | 229 | 3.82369 | 6800µF | 63V | - | 2000 Hrs @ 85°C | -40°C ~ 85°C | 6.8 | 63 | 1.778386846
493-7287-ND | CAP ALUM 3900UF 20% 63V SNAP | 94 | 2.19874 | 3900µF | 63V | - | 3000 Hrs @ 85°C | -40°C ~ 85°C | 3.9 | 63 | 1.773743144
1189-2904-ND | CAP ALUM 6800UF 20% 80V SNAP | 154 | 3.83963 | 6800µF | 80V | - | 3000 Hrs @ 85°C | -40°C ~ 85°C | 6.8 | 80 | 1.771003977
338-1985-ND | CAP ALUM 27000UF 20% 80V SNAP | 252 | 15.33394 | 27000µF | 80V | - | 3000 Hrs @ 85°C | -40°C ~ 85°C | 27 | 80 | 1.760799899
LLS1J472MELB-ND | CAP ALUM 4700UF 20% 63V SNAP | 196 | 2.67571 | 4700µF | 63V | - | 3000 Hrs @ 85°C | -40°C ~ 85°C | 4.7 | 63 | 1.756543123
493-12797-3-ND | CAP ALUM 1000UF 20% 63V RADIAL | 1750 | 0.57024 | 1000µF | 63V | - | 2000 Hrs @ 85°C | -40°C ~ 85°C | 1 | 63 | 1.753647587
493-13917-ND | CAP ALUM 4700UF 20% 80V SNAP | 378 | 2.68256 | 4700µF | 80V | - | 3000 Hrs @ 85°C | -40°C ~ 85°C | 4.7 | 80 | 1.752057736
338-2466-ND | CAP ALUM 6800UF 20% 80V SNAP | 953 | 3.88397 | 6800µF | 80V | 45 mOhm @ 120Hz | 3000 Hrs @ 85°C | -40°C ~ 85°C | 6.8 | 80 | 1.750785923
493-1135-ND | CAP ALUM 6800UF 20% 63V RADIAL | 521 | 3.89551 | 6800µF | 63V | - | 2000 Hrs @ 85°C | -40°C ~ 85°C | 6.8 | 63 | 1.745599421
338-2684-ND | CAP ALUM 10000UF 20% 63V SNAP | 279 | 5.73159 | 10000µF | 63V | 33 mOhm @ 120Hz | 3000 Hrs @ 85°C | -40°C ~ 85°C | 10 | 63 | 1.744716562
493-7173-ND | CAP ALUM 3300UF 20% 63V SNAP | 113 | 1.89407 | 3300µF | 63V | - | 3000 Hrs @ 105°C | -40°C ~ 105°C | 3.3 | 63 | 1.742279852
493-12477-ND | CAP ALUM 3300UF 20% 63V RADIAL | 261 | 1.89919 | 3300µF | 63V | - | 1000 Hrs @ 105°C | -55°C ~ 105°C | 3.3 | 63 | 1.737582864
565-2908-ND | CAP ALUM 3300UF 20% 63V SNAP | 158 | 1.90252 | 3300µF | 63V | 75 mOhm @ 120Hz | 2000 Hrs @ 105°C | -40°C ~ 105°C | 3.3 | 63 | 1.734541555
338-1653-ND | CAP ALUM 6800UF 20% 80V SNAP | 503 | 3.93893 | 6800µF | 80V | 49 mOhm | 3000 Hrs @ 85°C | -40°C ~ 85°C | 6.8 | 80 | 1.726357158
1189-3944-ND | CAP ALUM 5600UF 20% 63V SNAP-IN | 100 | 3.30338 | 5600µF | 63V | - | 2000 Hrs @ 105°C | -40°C ~ 105°C | 5.6 | 63 | 1.695233367
493-13916-ND | CAP ALUM 3900UF 20% 80V SNAP | 100 | 2.30206 | 3900µF | 80V | - | 3000 Hrs @ 85°C | -40°C ~ 85°C | 3.9 | 80 | 1.694134818
565-2913-ND | CAP ALUM 4700UF 20% 63V SNAP | 3430 | 2.77768 | 4700µF | 63V | 53 mOhm @ 120Hz | 2000 Hrs @ 105°C | -40°C ~ 105°C | 4.7 | 63 | 1.69205956
1189-2903-ND | CAP ALUM 4700UF 20% 80V SNAP | 459 | 2.78107 | 4700µF | 80V | - | 3000 Hrs @ 85°C | -40°C ~ 85°C | 4.7 | 80 | 1.689997016
338-2560-ND | CAP ALUM 5600UF 20% 63V SNAP | 2875 | 3.31603 | 5600µF | 63V | - | 3000 Hrs @ 105°C | -40°C ~ 105°C | 5.6 | 63 | 1.688766386
493-7181-ND | CAP ALUM 8200UF 20% 63V SNAP | 132 | 4.86784 | 8200µF | 63V | - | 3000 Hrs @ 105°C | -40°C ~ 105°C | 8.2 | 63 | 1.684525375
493-7286-ND | CAP ALUM 3300UF 20% 63V SNAP | 279 | 1.96264 | 3300µF | 63V | - | 3000 Hrs @ 85°C | -40°C ~ 85°C | 3.3 | 63 | 1.681408715
338-2315-ND | CAP ALUM 4700UF 20% 63V SNAP | 978 | 2.79672 | 4700µF | 63V | - | 3000 Hrs @ 105°C | -40°C ~ 105°C | 4.7 | 63 | 1.680540061
493-12412-ND | CAP ALUM 3300UF 20% 63V RADIAL | 147 | 1.96645 | 3300µF | 63V | - | 2000 Hrs @ 85°C | -40°C ~ 85°C | 3.3 | 63 | 1.678150983
338-1654-ND | CAP ALUM 6800UF 20% 80V SNAP | 1963 | 4.06717 | 6800µF | 80V | 49 mOhm | 3000 Hrs @ 85°C | -40°C ~ 85°C | 6.8 | 80 | 1.671924213
338-2455-ND | CAP ALUM 4700UF 20% 80V SNAP | 1613 | 2.81573 | 4700µF | 80V | 65 mOhm @ 120Hz | 3000 Hrs @ 85°C | -40°C ~ 85°C | 4.7 | 80 | 1.669194134
493-8470-ND | CAP ALUM 6800UF 20% 80V SNAP | 18 | 4.08549 | 6800µF | 80V | - | 3000 Hrs @ 105°C | -40°C ~ 105°C | 6.8 | 80 | 1.664427033
338-2462-ND | CAP ALUM 5600UF 20% 80V SNAP | 2133 | 3.37099 | 5600µF | 80V | 55 mOhm @ 120Hz | 3000 Hrs @ 85°C | -40°C ~ 85°C | 5.6 | 80 | 1.66123305
493-12476-ND | CAP ALUM 2200UF 20% 63V RADIAL | 595 | 1.33177 | 2200µF | 63V | - | 1000 Hrs @ 105°C | -55°C ~ 105°C | 2.2 | 63 | 1.651936896
4653PHBK-ND | CAP ALUM 6800UF 20% 63V SNAP | 38 | 4.14045 | 6800µF | 63V | 59 mOhm | 2000 Hrs @ 105°C | -40°C ~ 105°C | 6.8 | 63 | 1.642333563
493-8693-ND | CAP ALUM 10000UF 20% 63V SNAP | 51 | 6.09411 | 10000µF | 63V | - | 5000 Hrs @ 105°C | -40°C ~ 105°C | 10 | 63 | 1.6409287
338-2456-ND | CAP ALUM 4700UF 20% 80V SNAP | 422 | 2.89465 | 4700µF | 80V | 65 mOhm @ 120Hz | 3000 Hrs @ 85°C | -40°C ~ 85°C | 4.7 | 80 | 1.623685074
338-2108-ND | CAP ALUM 12000UF 20% 80V SNAP | 531 | 7.39266 | 12000µF | 80V | - | 3000 Hrs @ 85°C | -40°C ~ 85°C | 12 | 80 | 1.623231692
493-13915-ND | CAP ALUM 3300UF 20% 80V SNAP | 90 | 2.03571 | 3300µF | 80V | - | 3000 Hrs @ 85°C | -40°C ~ 85°C | 3.3 | 80 | 1.621056044
565-3979-ND | CAP ALUM 1800UF 20% 63V RADIAL | 629 | 1.11075 | 1800µF | 63V | - | 10000 Hrs @ 105°C | -40°C ~ 105°C | 1.8 | 63 | 1.620526671
493-1361-ND | CAP ALUM 3300UF 20% 63V RADIAL | 2942 | 2.04027 | 3300µF | 63V | - | 1000 Hrs @ 105°C | -55°C ~ 105°C | 3.3 | 63 | 1.617432987
338-3709-ND | CAP ALUM 3300UF 20% 63V SNAP | 1278 | 2.05473 | 3300µF | 63V | - | 3000 Hrs @ 105°C | -40°C ~ 105°C | 3.3 | 63 | 1.60605043
493-7285-ND | CAP ALUM 3300UF 20% 63V SNAP | 206 | 2.05758 | 3300µF | 63V | - | 3000 Hrs @ 85°C | -40°C ~ 85°C | 3.3 | 63 | 1.603825854
1189-3955-ND | CAP ALUM 6800UF 20% 80V SNAP-IN | 96 | 4.28024 | 6800µF | 80V | - | 3000 Hrs @ 85°C | -40°C ~ 85°C | 6.8 | 80 | 1.588695961
493-8690-ND | CAP ALUM 6800UF 20% 63V SNAP | 195 | 4.28098 | 6800µF | 63V | - | 5000 Hrs @ 105°C | -40°C ~ 105°C | 6.8 | 63 | 1.588421343
493-16172-ND | CAP ALUM 1000UF 20% 63V RADIAL | 540 | 0.62973 | 1000µF | 63V | - | 1000 Hrs @ 105°C | -55°C ~ 105°C | 1 | 63 | 1.587982151
493-1359-ND | CAP ALUM 1000UF 20% 63V RADIAL | 10550 | 0.63079 | 1000µF | 63V | - | 1000 Hrs @ 105°C | -55°C ~ 105°C | 1 | 63 | 1.585313654
338-1984-ND | CAP ALUM 22000UF 20% 80V SNAP | 68 | 13.88884 | 22000µF | 80V | - | 3000 Hrs @ 85°C | -40°C ~ 85°C | 22 | 80 | 1.584005576
493-12585-3-ND | CAP ALUM 1000UF 20% 63V RADIAL | 500 | 0.63609 | 1000µF | 63V | - | 2000 Hrs @ 85°C | -40°C ~ 85°C | 1 | 63 | 1.572104576
493-10689-ND | CAP ALUM 6800UF 20% 63V RADIAL | 3 | 4.34327 | 6800µF | 63V | - | 2000 Hrs @ 85°C | -40°C ~ 85°C | 6.8 | 63 | 1.565640635
338-2703-ND | CAP ALUM 4700UF 20% 63V SNAP | 6651 | 3.00458 | 4700µF | 63V | 80 mOhm @ 120Hz | 3000 Hrs @ 85°C | -40°C ~ 85°C | 4.7 | 63 | 1.564278535
493-1131-ND | CAP ALUM 3300UF 20% 63V RADIAL | 1027 | 2.11085 | 3300µF | 63V | - | 2000 Hrs @ 85°C | -40°C ~ 85°C | 3.3 | 63 | 1.563351257
493-8692-ND | CAP ALUM 8200UF 20% 63V SNAP | 143 | 5.25043 | 8200µF | 63V | - | 5000 Hrs @ 105°C | -40°C ~ 105°C | 8.2 | 63 | 1.561776845
399-6530-ND | CAP ALUM 6800UF 20% 63V SNAP | 194 | 4.36342 | 6800µF | 63V | - | 2000 Hrs @ 105°C | -40°C ~ 105°C | 6.8 | 63 | 1.558410605
493-7180-ND | CAP ALUM 6800UF 20% 63V SNAP | 200 | 4.36909 | 6800µF | 63V | - | 3000 Hrs @ 105°C | -40°C ~ 105°C | 6.8 | 63 | 1.556388172
493-8443-ND | CAP ALUM 2700UF 20% 63V SNAP | 207 | 1.73623 | 2700µF | 63V | - | 3000 Hrs @ 105°C | -40°C ~ 105°C | 2.7 | 63 | 1.555093507
565-2911-ND | CAP ALUM 3900UF 20% 63V SNAP | 401 | 2.53036 | 3900µF | 63V | 64 mOhm @ 120Hz | 2000 Hrs @ 105°C | -40°C ~ 105°C | 3.9 | 63 | 1.541282663
493-14392-ND | CAP ALUM 10000UF 20% 80V SNAP | 376 | 6.49258 | 10000µF | 80V | - | 3000 Hrs @ 85°C | -40°C ~ 85°C | 10 | 80 | 1.540219759
493-1360-ND | CAP ALUM 2200UF 20% 63V RADIAL | 16116 | 1.42864 | 2200µF | 63V | - | 1000 Hrs @ 105°C | -55°C ~ 105°C | 2.2 | 63 | 1.539926084
338-1630-ND | CAP ALUM 4700UF 20% 80V SNAP | 1295 | 3.05954 | 4700µF | 80V | 71 mOhm | 3000 Hrs @ 85°C | -40°C ~ 85°C | 4.7 | 80 | 1.536178641
338-1610-ND | CAP ALUM 3300UF 20% 80V SNAP | 1198 | 2.16888 | 3300µF | 80V | 101 mOhm | 3000 Hrs @ 85°C | -40°C ~ 85°C | 3.3 | 80 | 1.521522629
493-11030-ND | CAP ALUM 3300UF 20% 63V RADIAL | 16 | 2.16925 | 3300µF | 63V | - | 2000 Hrs @ 85°C | -40°C ~ 85°C | 3.3 | 63 | 1.521263109
338-2450-ND | CAP ALUM 3900UF 20% 80V SNAP | 175 | 2.56841 | 3900µF | 80V | 80 mOhm @ 120Hz | 3000 Hrs @ 85°C | -40°C ~ 85°C | 3.9 | 80 | 1.518449157
493-10711-ND | CAP ALUM 2200UF 20% 63V RADIAL | 163 | 1.45015 | 2200µF | 63V | - | 2000 Hrs @ 85°C | -40°C ~ 85°C | 2.2 | 63 | 1.51708444
493-1960-ND | CAP ALUM 2200UF 20% 63V RADIAL | 24235 | 1.4535 | 2200µF | 63V | - | 8000 Hrs @ 105°C | -55°C ~ 105°C | 2.2 | 63 | 1.513587891
493-11151-ND | CAP ALUM 2200UF 20% 63V RADIAL | 87 | 1.4535 | 2200µF | 63V | - | 3000 Hrs @ 105°C | -55°C ~ 105°C | 2.2 | 63 | 1.513587891
338-1498-ND | CAP ALUM 3300UF 20% 63V SNAP | 615 | 2.18791 | 3300µF | 63V | 121 mOhm | 3000 Hrs @ 105°C | -40°C ~ 105°C | 3.3 | 63 | 1.508288732
493-10696-ND | CAP ALUM 4700UF 20% 63V RADIAL | 128 | 3.13136 | 4700µF | 63V | - | 2000 Hrs @ 85°C | -40°C ~ 85°C | 4.7 | 63 | 1.500945276
338-3710-ND | CAP ALUM 3900UF 20% 63V SNAP | 141 | 2.60646 | 3900µF | 63V | - | 3000 Hrs @ 105°C | -40°C ~ 105°C | 3.9 | 63 | 1.496282314
493-13914-ND | CAP ALUM 3300UF 20% 80V SNAP | 226 | 2.20693 | 3300µF | 80V | - | 3000 Hrs @ 85°C | -40°C ~ 85°C | 3.3 | 80 | 1.495289837
565-2909-ND | CAP ALUM 3300UF 20% 63V SNAP | 348 | 2.20693 | 3300µF | 63V | 75 mOhm @ 120Hz | 2000 Hrs @ 105°C | -40°C ~ 105°C | 3.3 | 63 | 1.495289837
493-14772-ND | CAP ALUM 4700UF 20% 80V SNAP | 191 | 3.16012 | 4700µF | 80V | - | 3000 Hrs @ 85°C | -40°C ~ 85°C | 4.7 | 80 | 1.487285293
338-3844-ND | CAP ALUM 3900UF 20% 80V SNAP | 922 | 2.62548 | 3900µF | 80V | 85 mOhm | 3000 Hrs @ 85°C | -40°C ~ 85°C | 3.9 | 80 | 1.485442662
493-8688-ND | CAP ALUM 5600UF 20% 63V SNAP | 2 | 3.78266 | 5600µF | 63V | - | 5000 Hrs @ 105°C | -40°C ~ 105°C | 5.6 | 63 | 1.480439691
1189-3943-ND | CAP ALUM 3300UF 20% 63V SNAP-IN | 200 | 2.24421 | 3300µF | 63V | - | 2000 Hrs @ 105°C | -40°C ~ 105°C | 3.3 | 63 | 1.470450626
338-2269-ND | CAP ALUM 5600UF 20% 80V SNAP | 557 | 3.81068 | 5600µF | 80V | 55 mOhm @ 120Hz | 3000 Hrs @ 85°C | -40°C ~ 85°C | 5.6 | 80 | 1.46955399
338-2110-ND | CAP ALUM 15000UF 20% 80V SNAP | 147 | 10.24021 | 15000µF | 80V | - | 3000 Hrs @ 85°C | -40°C ~ 85°C | 15 | 80 | 1.46481371
493-7284-ND | CAP ALUM 2700UF 20% 63V SNAP | 131 | 1.84651 | 2700µF | 63V | - | 3000 Hrs @ 85°C | -40°C ~ 85°C | 2.7 | 63 | 1.462217914
399-6060-ND | CAP ALUM 2200UF 20% 63V SNAP | 597 | 1.51052 | 2200µF | 63V | - | 2000 Hrs @ 105°C | -25°C ~ 105°C | 2.2 | 63 | 1.456452083
493-7177-ND | CAP ALUM 4700UF 20% 63V SNAP | 81 | 3.24275 | 4700µF | 63V | - | 3000 Hrs @ 105°C | -40°C ~ 105°C | 4.7 | 63 | 1.449387094
338-2109-ND | CAP ALUM 12000UF 20% 80V SNAP | 50 | 8.28708 | 12000µF | 80V | - | 3000 Hrs @ 85°C | -40°C ~ 85°C | 12 | 80 | 1.448037186
493-15150-ND | CAP ALUM 1000UF 20% 63V RADIAL | 295 | 0.69146 | 1000µF | 63V | - | 2000 Hrs @ 85°C | -40°C ~ 85°C | 1 | 63 | 1.446215255
493-10703-ND | CAP ALUM 3300UF 20% 63V RADIAL | 9 | 2.29122 | 3300µF | 63V | - | 2000 Hrs @ 85°C | -40°C ~ 85°C | 3.3 | 63 | 1.440280724
1189-2870-ND | CAP ALUM 3300UF 20% 80V SNAP | 175 | 2.30053 | 3300µF | 80V | - | 3000 Hrs @ 85°C | -40°C ~ 85°C | 3.3 | 80 | 1.434452061
493-8689-ND | CAP ALUM 5600UF 20% 63V SNAP | 198 | 3.90724 | 5600µF | 63V | - | 5000 Hrs @ 105°C | -40°C ~ 105°C | 5.6 | 63 | 1.43323676
493-7175-ND | CAP ALUM 3900UF 20% 63V SNAP | 123 | 2.7246 | 3900µF | 63V | - | 3000 Hrs @ 105°C | -40°C ~ 105°C | 3.9 | 63 | 1.431402775
493-8444-ND | CAP ALUM 2700UF 20% 63V SNAP | 176 | 1.89407 | 2700µF | 63V | - | 3000 Hrs @ 105°C | -40°C ~ 105°C | 2.7 | 63 | 1.425501697
338-3809-ND | CAP ALUM 3300UF 20% 80V SNAP | 2629 | 2.34011 | 3300µF | 80V | 101 mOhm | 3000 Hrs @ 85°C | -40°C ~ 85°C | 3.3 | 80 | 1.410190119
338-2321-ND | CAP ALUM 5600UF 63V 20% SNAP | 783 | 3.99389 | 5600µF | 63V | - | 3000 Hrs @ 105°C | -40°C ~ 105°C | 5.6 | 63 | 1.402141772
493-6173-ND | CAP ALUM 6800UF 20% 100V SNAP | 596 | 4.85543 | 6800µF | 100V | - | 3000 Hrs @ 85°C | -40°C ~ 85°C | 6.8 | 100 | 1.40049388
338-3819-ND | CAP ALUM 2700UF 20% 63V SNAP | 2194 | 1.93353 | 2700µF | 63V | - | 3000 Hrs @ 105°C | -40°C ~ 105°C | 2.7 | 63 | 1.396409676
338-2039-ND | CAP ALUM 27000UF 20% 80V SNAP | 37 | 19.4455 | 27000µF | 80V | 18 mOhm | 3000 Hrs @ 105°C | -40°C ~ 105°C | 27 | 80 | 1.388496053
493-8683-ND | CAP ALUM 3900UF 20% 63V SNAP | 97 | 2.81112 | 3900µF | 63V | - | 5000 Hrs @ 105°C | -40°C ~ 105°C | 3.9 | 63 | 1.387347392
493-13365-ND | CAP ALUM 10000UF 20% 63V SNAP | 142 | 7.25905 | 10000µF | 63V | - | 1000 Hrs @ 85°C | -40°C ~ 85°C | 10 | 63 | 1.377590732
493-7170-ND | CAP ALUM 2200UF 20% 63V SNAP | 100 | 1.59812 | 2200µF | 63V | - | 3000 Hrs @ 105°C | -40°C ~ 105°C | 2.2 | 63 | 1.376617526
1189-3356-ND | CAP ALUM 3300UF 20% 63V SNAP | 186 | 2.41392 | 3300µF | 63V | - | 2000 Hrs @ 105°C | -40°C ~ 105°C | 3.3 | 63 | 1.367070988
565-2039-ND | CAP ALUM 1800UF 20% 63V RADIAL | 3676 | 1.31796 | 1800µF | 63V | - | 8000 Hrs @ 105°C | -55°C ~ 105°C | 1.8 | 63 | 1.365747064
338-2712-ND | CAP ALUM 8200UF 20% 63V SNAP | 740 | 6.0054 | 8200µF | 63V | 67 mOhm @ 120Hz | 3000 Hrs @ 85°C | -40°C ~ 85°C | 8.2 | 63 | 1.365437773
338-2028-ND | CAP ALUM 18000UF 20% 63V SNAP | 29 | 13.19727 | 18000µF | 63V | 23 mOhm | 3000 Hrs @ 105°C | -40°C ~ 105°C | 18 | 63 | 1.363918447
338-1481-ND | CAP ALUM 2200UF 20% 63V SNAP | 4642 | 1.61785 | 2200µF | 63V | 181 mOhm | 3000 Hrs @ 105°C | -40°C ~ 105°C | 2.2 | 63 | 1.359829403
493-8687-ND | CAP ALUM 4700UF 20% 63V SNAP | 979 | 3.46022 | 4700µF | 63V | - | 5000 Hrs @ 105°C | -40°C ~ 105°C | 4.7 | 63 | 1.358295137
493-1959-ND | CAP ALUM 1500UF 20% 63V RADIAL | 2987 | 1.10685 | 1500µF | 63V | - | 8000 Hrs @ 105°C | -55°C ~ 105°C | 1.5 | 63 | 1.355197181
338-2538-ND | CAP ALUM 2700UF 20% 63V SNAP | 2046 | 1.99766 | 2700µF | 63V | - | 3000 Hrs @ 105°C | -40°C ~ 105°C | 2.7 | 63 | 1.35158135
1189-3853-ND | CAP ALUM 12000UF 20% 63V SNAP | 100 | 8.92632 | 12000µF | 63V | - | 2000 Hrs @ 105°C | -40°C ~ 105°C | 12 | 63 | 1.344338989
565-2718-ND | CAP ALUM 6800UF 20% 100V SNAP | 99 | 5.07447 | 6800µF | 100V | 37 mOhm @ 120Hz | 2000 Hrs @ 85°C | -40°C ~ 85°C | 6.8 | 100 | 1.340041423
565-2906-ND | CAP ALUM 2700UF 20% 63V SNAP | 295 | 2.01667 | 2700µF | 63V | 92 mOhm @ 120Hz | 2000 Hrs @ 105°C | -40°C ~ 105°C | 2.7 | 63 | 1.338840762
1189-3357-ND | CAP ALUM 4700UF 20% 63V SNAP | 147 | 3.51609 | 4700µF | 63V | - | 2000 Hrs @ 105°C | -40°C ~ 105°C | 4.7 | 63 | 1.336712086
338-2106-ND | CAP ALUM 10000UF 20% 80V SNAP | 166 | 7.48393 | 10000µF | 80V | - | 3000 Hrs @ 85°C | -40°C ~ 85°C | 10 | 80 | 1.336196357
1189-3854-ND | CAP ALUM 5600UF 20% 63V SNAP | 100 | 4.19322 | 5600µF | 63V | - | 2000 Hrs @ 105°C | -40°C ~ 105°C | 5.6 | 63 | 1.335489194
565-2904-ND | CAP ALUM 2200UF 20% 63V SNAP | 379 | 1.64744 | 2200µF | 63V | 113 mOhm @ 120Hz | 2000 Hrs @ 105°C | -40°C ~ 105°C | 2.2 | 63 | 1.335405235
493-8684-ND | CAP ALUM 3900UF 20% 63V SNAP | 146 | 2.92983 | 3900µF | 63V | - | 5000 Hrs @ 105°C | -40°C ~ 105°C | 3.9 | 63 | 1.331135254
493-6171-ND | CAP ALUM 4700UF 20% 100V SNAP | 92 | 3.53587 | 4700µF | 100V | - | 3000 Hrs @ 85°C | -40°C ~ 85°C | 4.7 | 100 | 1.329234389
493-1658-ND | CAP ALUM 1500UF 20% 63V RADIAL | 620 | 1.13605 | 1500µF | 63V | - | 10000 Hrs @ 105°C | -40°C ~ 105°C | 1.5 | 63 | 1.320364421
493-8680-ND | CAP ALUM 3300UF 20% 63V SNAP | 51 | 2.50314 | 3300µF | 63V | - | 5000 Hrs @ 105°C | -40°C ~ 105°C | 3.3 | 63 | 1.31834416
1189-1473-ND | CAP ALUM 1000UF 20% 63V RADIAL | 1154 | 0.75932 | 1000µF | 63V | - | 2000 Hrs @ 105°C | -55°C ~ 105°C | 1 | 63 | 1.316967813
399-6075-ND | CAP ALUM 4700UF 20% 80V SNAP | 345 | 3.58387 | 4700µF | 80V | - | 2000 Hrs @ 85°C | -40°C ~ 85°C | 4.7 | 80 | 1.311431497
1189-1505-ND | CAP ALUM 2200UF 20% 63V RADIAL | 9792 | 1.6798 | 2200µF | 63V | - | 10000 Hrs @ 105°C | -40°C ~ 105°C | 2.2 | 63 | 1.309679724
493-7312-ND | CAP ALUM 5600UF 20% 100V SNAP | 36 | 4.30534 | 5600µF | 100V | - | 3000 Hrs @ 85°C | -40°C ~ 85°C | 5.6 | 100 | 1.300710281
338-2031-ND | CAP ALUM 8200UF 20% 80V SNAP | 1 | 6.31571 | 8200µF | 80V | - | 3000 Hrs @ 105°C | -40°C ~ 105°C | 8.2 | 80 | 1.298349671
338-2107-ND | CAP ALUM 10000UF 20% 80V SNAP | 93 | 7.73948 | 10000µF | 80V | - | 3000 Hrs @ 85°C | -40°C ~ 85°C | 10 | 80 | 1.29207647
LLS1J222MELA-ND | CAP ALUM 2200UF 20% 63V SNAP | 5965 | 1.70348 | 2200µF | 63V | - | 3000 Hrs @ 85°C | -40°C ~ 85°C | 2.2 | 63 | 1.291473924
493-7172-ND | CAP ALUM 3300UF 20% 63V SNAP | 511 | 2.56194 | 3300µF | 63V | - | 3000 Hrs @ 105°C | -40°C ~ 105°C | 3.3 | 63 | 1.288086372
338-1590-ND | CAP ALUM 2200UF 20% 80V SNAP | 354 | 1.7165 | 2200µF | 80V | 151 mOhm | 3000 Hrs @ 85°C | -40°C ~ 85°C | 2.2 | 80 | 1.281677833
493-8681-ND | CAP ALUM 3300UF 20% 63V SNAP | 3 | 2.58496 | 3300µF | 63V | - | 5000 Hrs @ 105°C | -40°C ~ 105°C | 3.3 | 63 | 1.276615499
493-7283-ND | CAP ALUM 2200UF 20% 63V SNAP | 74 | 1.72933 | 2200µF | 63V | - | 3000 Hrs @ 85°C | -40°C ~ 85°C | 2.2 | 63 | 1.27216899
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

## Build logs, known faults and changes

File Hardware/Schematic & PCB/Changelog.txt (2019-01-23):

0.1.0   Craig Comberbach    2017
Initial version
Designed to be milled out

0.1.1   Craig Comberbach    2017
Modernized for use with board house standards

0.1.2   Craig Comberbach    2017
Fixed the Drain/Source reversal on Input/Output H-Bridges
Fixed the +/- inputs on Current Sense amplifer
Fixed the TQFP-64 breakout board header
Swapped Current Sense amplifier sub-components to aide in routing
Add a 100nF capacitor to the MCLR line
Layed the board out to be laser milled
Removed unnecesary safety logic
Removed Debug RX line
Increased Isense resistors to 3mR (Input) and 33mR (Output)
Replaced battery headers with battery holders
Added a DPST switch to disconnect both power sources if needed
Added Bypass cap for Current Sense amplifier
H-Bridge Control Lines A_IN and B_IN swapped micro pins
H-Bridge Control Lines C_IN and D_IN moved micro pins
Switched Grounds 1, 2, 3, 4, and 5 moved micro pins
Vsense (-T1.P) and Vsense (+Vsolar) swapped micro pins

0.1.3   Craig Comberbach    2017-07-09
Doubled up H-Bridge FETs to improve efficiency and decrease thermal load on H-Bridge FETs
H-Bridge drivers now control one side instead of kitty corner
 -Reduces inductance/ringing on control lines
H-Bridge drivers now have two signal lines instead of one
Each bridge has four control lines now instead of just two
Removed ultimately ineffective but expensive 1uF 250V ceramic capacitors from the H-Bridges
Added by-pass caps to all analog inputs
H-Bridge Drivers now have 44uF (2x 22uF) bootstrap capacitors
Added a 5V buck SMPS to convert incoming voltage to provide a conditioned input for the 3.3V linear and 15V boost SMPS
Added a 15V boost SMPS to convert 5VDC into the voltage required to power the H-Bridge drivers
Fixed HVGND so that it references the rest of the circuit correctly
Removed the DC- voltage rail sensor as it became circuit ground
Added a 6th Temperature sensor as there was a free analog pin

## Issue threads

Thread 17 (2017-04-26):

ADC buffers consistently filling out of order

CraigComberbach, 2017-04-26:
The buffers are not filling sequentially as expected. I have added an extra tab on the ones that I have identified to be matched correctly (even if out of order).

Why are they out of order?
Are the ones without an extra tab aligned correctly?
What was overlooked? I've never experienced this issue before, and I have done lots of ADC work.

Closed 2019-01-23.

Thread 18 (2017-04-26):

ADC channels can be triggered independently

CraigComberbach, 2017-04-26:
Currently triggering a scan causes all of the channels to be read. This works great if we have a single stage inverter and we are sampling at the peaks. The only time this is not optimal is when you have two inverters running at different frequencies or phase shifted such that the code is being called on the peak of one, but not on the other. The code currently assumes everything is at the peak and is processing the new values accordingly.

This obviously leads to some rather confusing readings as the measurement is not taken at a peak, but is system variables are calculated as if it was.

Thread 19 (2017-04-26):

Proper voltage control

CraigComberbach, 2017-04-26:
Currently the code does a simple step and hold to control the output voltage. The reaction time can be abysmal when given a step function. For example, on startup, tracking to 40VDC at 20Hz can take as long as a second. This timing can be sped up by preloading expected starting values, and increasing the slew rate limiting on the feedback voltage. These can lead to accidental over-voltage and instability in output voltage.

Ideally we would lock on much quicker using Mikes formulaes.

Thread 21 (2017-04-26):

Thermistor table is currently a place holder

CraigComberbach, 2017-04-26:
The table is a place holder counting from 0 to 1023 (entire range of ADC). The real temperature values for each step have not been precalculated.

The future table should have a minimum of 1 decimal place of accuracy and be shifted so that it returns a number that is easy to do integer arithmetic on. ie 5.2ºC would be entered as the number 52.

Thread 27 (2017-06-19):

Address error when target frequency is 15Hz

CraigComberbach, 2017-06-19:
14, 16, and 17Hz specifically work (the rest also appears to work), only 15Hz causes an address error causing the code to enter one of the traps.

I haven't found a solution to it, but I did put a kludge into the pot reading mechanism that skips over that value if detected.

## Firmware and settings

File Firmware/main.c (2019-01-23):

/**************************************************************************************************
Target Hardware:		PIC24FJ256GA106
Code assumptions:		
Purpose:				Firmware for Afriji Solar DC to AC appliance power supply device
Notes:					

Version History:
v0.0.A	2017-03-12      Craig Comberbach, Michael MacKay
Compiler: XC16 v1.26	IDE: MPLABx 3.30	Tool: ICD3	Computer: Intel Core2 Quad CPU 2.40 GHz, 5 GB RAM, Windows 10 64 bit Home
 Revision History:
 * v0.0.A   -   Initial prototype firmware
**************************************************************************************************/
/*************    Header Files    ***************/
#include "Config.h"
#include "Scheduler.h"
#include "A2D.h"
#include "Inverter.h"
#include "Pins.h"
#include "Debug.h"

/************* Library Definition ***************/
/************* Semantic Versioning***************/
#if MAJOR_FIRMWARE_VERSION != 0
    #error "Firmware has had a change that loses some previously supported functionality"
#elif MINOR_FIRMWARE_VERSION != 1
    #error "Firmware has new features that this code may benefit from"
#elif PATCH_FIRMWARE_VERSION != 0
	#error "Firmware has had a bug fix, you should check to see that we weren't relying on a bug for functionality"
#endif
/*************Library Dependencies***************/
/************Arbitrary Functionality*************/
/*************   Magic  Numbers   ***************/
/*************    Enumeration     ***************/
/***********  Structure Definitions  ************/
/***********State Machine Definitions************/
/*************  Global Variables  ***************/
/*************Interrupt Prototypes***************/
/*************Function  Prototypes***************/
/************* Device Definitions ***************/
/************* Module Definitions ***************/
/************* Other  Definitions ***************/

_CONFIG1( JTAGEN_OFF & GCP_OFF & GWRP_OFF & BKBUG_OFF & COE_OFF & ICS_PGx3 & FWDTEN_ON & WINDIS_OFF & FWPSA_PR32 & WDTPS_PS1024 )
_CONFIG2( IESO_OFF & FNOSC_FRCPLL & FCKSM_CSDCMD & OSCIOFNC_ON & IOL1WAY_ON & POSCMOD_NONE )
_CONFIG3( WPDIS_WPDIS )

int main(void)
{
	ClrWdt();
	Configure_For_Afriji();

	//Scheduled Tasks
	Initialize_Scheduler(500/*uS*/);
	Schedule_Task(STARTUP_TASK,			&Heart_Beat_Task,	1000/*uS Delay*/,		50000/*uS Period*/,		20/*Repetitions*/);
	Schedule_Task(HEART_BEAT_TASK,		&Heart_Beat_Task,	1000000/*uS Delay*/,	500000/*uS Period*/,	PERMANENT_TASK);
	Schedule_Task(INVERTER_TASK,		&Inverter_Routine,	1000000/*uS Delay*/,	500/*uS Period*/,		PERMANENT_TASK);
	Schedule_Task(A2D_TASK,				&A2D_Routine,		16667/*uS Delay*/,		16667/*uS Period*/,		PERMANENT_TASK);//No longer than once ever 8mS will allow the result to be captured in time to be used with a 60Hz waveform
	Schedule_Task(FREQUENCY_RAMP_TASK,	&Frequency_Ramp,	2500000/*uS Delay*/,	500000/*uS Period*/,	40/*Repetitions*/);
	Schedule_Task(TERMINAL_TASK,		&Debug_Routine,		200000/*uS Delay*/,		100000/*uS Period*/,	1);

	while(1)
	{
		ClrWdt();
		while(Waiting_To_Run_Tasks())
		{
			ClrWdt();
			Task_Master();
			ClrWdt();
		}
		ClrWdt();
	}

	return 1;
}

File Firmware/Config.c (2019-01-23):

/**************************************************************************************************
Authours:				Craig Comberbach
Target Hardware:		PIC
Chip resources used:
Code assumptions:
Purpose:

Version History:
v0.0.0	2013-07-11  Craig Comberbach
	Compiler: C30 v3.31		IDE: MPLABx 1.80	Tool: RealICE	Computer: Intel Xeon CPU 3.07 GHz, 6 GB RAM, Windows 7 64 bit Professional SP1
	First version
**************************************************************************************************/
/*************    Header Files    ***************/
#include "Config.h"
#include "Pins.h"
#include "A2D.h"
#include "Scheduler.h"
#include "Analogs.h"
#include "Inverter.h"
#include "Debug.h"

/*************Semantic  Versioning***************/
/*************Library Dependencies***************/
#ifndef PINS_LIBRARY
	#error "You need to include the Pins library for this code to compile"
#endif

#ifndef A2D_LIBRARY
	#error "You need to include the A2D library for this code to compile"
#endif

#ifndef INVERTER_LIBRARY
	#error "You need to include the Inverter library for this code to compile"
#endif

#ifndef SCHEDULER_LIBRARY
	#error "You need to include the Scheduler library for this code to compile"
#endif

/************Arbitrary Functionality*************/
/*************   Magic  Numbers   ***************/
/***********State Machine Definitions*************/
/*************  Global Variables  ***************/
volatile int dummy;
const char compiledOnDate[] = __DATE__;
const char compiledAtTime[] = __TIME__;

/*************Function  Prototypes***************/
void __attribute__((interrupt, auto_psv)) _OscillatorFail(void);
void __attribute__((interrupt, auto_psv)) _AddressError(void);
void __attribute__((interrupt, auto_psv)) _StackError(void);
void __attribute__((interrupt, auto_psv)) _MathError(void);
void __attribute__((interrupt, auto_psv)) _DefaultInterrupt(void);

/************* Device Definitions ***************/
/************* Module Definitions ***************/
/************* Other  Definitions ***************/

void Configure_For_Afriji(void)
{
	/*************       Clock        ***************/
	CLKDIVbits.RCDIV	= 0;
	OSCTUNbits.TUN		= 0b000001; //+0.77%

	/*************        Pins        ***************/
	//PORTB
	Pin_Definition(PIN_RB0_TRANSFORMER_PRIMARY_MINUS,	Rx0, &TRISB, &ODCB, &LATB, &PORTB);	//RB0
	Pin_Definition(PIN_RB1_TRANSFORMER_PRIMARY_PLUS,	Rx1, &TRISB, &ODCB, &LATB, &PORTB);	//RB1
	Pin_Definition(PIN_RB2_VSOLAR_PLUS,					Rx2, &TRISB, &ODCB, &LATB, &PORTB);	//RB2
	Pin_Definition(PIN_RB3_TEMP2,						Rx3, &TRISB, &ODCB, &LATB, &PORTB);	//RB3
//	Pin_Definition(PIN_RB4_PGD,							Rx4, &TRISB, &ODCB, &LATB, &PORTB);	//RB4
//	Pin_Definition(PIN_RB5_PGC,							Rx5, &TRISB, &ODCB, &LATB, &PORTB);	//RB5
	Pin_Definition(PIN_RB6_TEMP1,						Rx6, &TRISB, &ODCB, &LATB, &PORTB);	//RB6
	Pin_Definition(PIN_RB7_TEMP3,						Rx7, &TRISB, &ODCB, &LATB, &PORTB);	//RB7
	Pin_Definition(PIN_RB8_TEMP4,						Rx8, &TRISB, &ODCB, &LATB, &PORTB);	//RB8
	Pin_Definition(PIN_RB9_INPUT_CURRENT,				Rx9, &TRISB, &ODCB, &LATB, &PORTB);	//RB9
	Pin_Definition(PIN_RB10_OUTPUT_CURRENT,				Rx10, &TRISB, &ODCB, &LATB, &PORTB);//RB10
	Pin_Definition(PIN_RB11_TEMP5,						Rx11, &TRISB, &ODCB, &LATB, &PORTB);//RB11
	Pin_Definition(PIN_RB12_VDC_BUS_PLUS,				Rx12, &TRISB, &ODCB, &LATB, &PORTB);//RB12
	Pin_Definition(PIN_RB13_TRANSFORMER_SECONDARY_PLUS,	Rx13, &TRISB, &ODCB, &LATB, &PORTB);//RB13
	Pin_Definition(PIN_RB14_VOUT_PLUS,					Rx14, &TRISB, &ODCB, &LATB, &PORTB);//RB14
	Pin_Definition(PIN_RB15_VOUT_MINUS,					Rx15, &TRISB, &ODCB, &LATB, &PORTB);//RB15
	//PORTC
	Pin_Definition(PIN_RC12,							Rx12, &TRISC, &ODCC, &LATC, &PORTC);//RC12
	Pin_Definition(PIN_RC13,							Rx13, &TRISC, &ODCC, &LATC, &PORTC);//RC13
	Pin_Definition(PIN_RC14,							Rx14, &TRISC, &ODCC, &LATC, &PORTC);//RC14
	Pin_Definition(PIN_RC15,							Rx15, &TRISC, &ODCC, &LATC, &PORTC);//RC15
	//PORTD
	Pin_Definition(PIN_RD0_HOB_HiA,						Rx0, &TRISD, &ODCD, &LATD, &PORTD);	//RD0
	Pin_Definition(PIN_RD1_TERMINAL_TX,					Rx1, &TRISD, &ODCD, &LATD, &PORTD);	//RD1
	Pin_Definition(PIN_RD2,								Rx2, &TRISD, &ODCD, &LATD, &PORTD);	//RD2
	Pin_Definition(PIN_RD3,								Rx3, &TRISD, &ODCD, &LATD, &PORTD);	//RD3
	Pin_Definition(PIN_RD4_LOB_HiA,						Rx4, &TRISD, &ODCD, &LATD, &PORTD);	//RD4
	Pin_Definition(PIN_RD5_LOA_HiA,						Rx5, &TRISD, &ODCD, &LATD, &PORTD);	//RD5
	Pin_Definition(PIN_RD6,								Rx6, &TRISD, &ODCD, &LATD, &PORTD);	//RD6
	Pin_Definition(PIN_RD7,								Rx7, &TRISD, &ODCD, &LATD, &PORTD);	//RD7
	Pin_Definition(PIN_RD8_HOA_HiA,						Rx8, &TRISD, &ODCD, &LATD, &PORTD);	//RD8
	Pin_Definition(PIN_RD9_GREEN_LED,					Rx9, &TRISD, &ODCD, &LATD, &PORTD);	//RD9
	Pin_Definition(PIN_RD10_RED_LED,					Rx10, &TRISD, &ODCD, &LATD, &PORTD);//RD10
	Pin_Definition(PIN_RD11_BLUE_LED,					Rx11, &TRISD, &ODCD, &LATD, &PORTD);//RD11
	//PORTE
	Pin_Definition(PIN_RE0,								Rx0, &TRISE, &ODCE, &LATE, &PORTE);	//RE0
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

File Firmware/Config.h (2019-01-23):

#ifndef CONFIG_H
#define	CONFIG_H

//Hardware specific include file
#include <p24FJ256GA106.h>
#include <stdint.h>

//System Variables
#define HiI_INVERTER_ENABLED
#define HiV_INVERTER_ENABLED
//#define	TERMINAL_WINDOW_DEBUG_ENABLED

//Clock Frequency
#define FOSC_Hz			32000000			//32MHz
#define TOSC_ps			31250				//32MHz
#define FOSC_kHz		FOSC_Hz/1000		//32MHz
#define TOSC_ns			TOSC_ps/1000		//32MHz
#define FOSC_MHz		FOSC_kHz/1000		//32MHz
#define TOSC_us			TOSC_ns/1000		//32MHz
#define FCY_Hz			FOSC_Hz/2			//16MHz
#define TCY_ps			TOSC_ps*2			//16MHz
#define FCY_kHz			FCY_Hz/1000			//16MHz
#define TCY_ns			TCY_ps/1000			//16MHz
#define FCY_MHz			FCY_kHz/1000		//16MHz
#define TCY_us			TCY_ns/1000			//16MHz

//Compiled information
extern const char compiledOnDate[];
extern const char compiledAtTime[];
#define MAJOR_FIRMWARE_VERSION	0
#define MINOR_FIRMWARE_VERSION	1
#define PATCH_FIRMWARE_VERSION	0

enum SCHEDULER_DEFINITIONS
{
	STARTUP_TASK,
	HEART_BEAT_TASK,
	INVERTER_TASK,
	A2D_TASK,
	FREQUENCY_RAMP_TASK,
	TERMINAL_TASK,
	NUMBER_OF_SCHEDULED_TASKS
};

enum INVERTERS_SUPPORTED
{
	#ifdef HiI_INVERTER_ENABLED
	HIGH_CURRENT_INVERTER,
	#endif
	#ifdef HiV_INVERTER_ENABLED
	HIGH_VOLTAGE_INVERTER,
	#endif
	NUMBER_OF_INVERTERS_SUPPORTED
};

//Pins
enum PIN_DEFINITIONS
{
	//PORTB
	PIN_RB0_TRANSFORMER_PRIMARY_MINUS,		//RB0
	PIN_RB1_TRANSFORMER_PRIMARY_PLUS,		//RB1
	PIN_RB2_VSOLAR_PLUS,					//RB2
	PIN_RB3_TEMP2,							//RB3
	PIN_RB4_PGD,							//RB4 - PGD
	PIN_RB5_PGC,							//RB5 - PGC
	PIN_RB6_TEMP1,							//RB6
	PIN_RB7_TEMP3,							//RB7
	PIN_RB8_TEMP4,							//RB8
	PIN_RB9_INPUT_CURRENT,					//RB9
	PIN_RB10_OUTPUT_CURRENT,				//RB10
	PIN_RB11_TEMP5,							//RB11
	PIN_RB12_VDC_BUS_PLUS,					//RB12
	PIN_RB13_TRANSFORMER_SECONDARY_PLUS,	//RB13
	PIN_RB14_VOUT_PLUS,						//RB14
	PIN_RB15_VOUT_MINUS,					//RB15
	//PORTC
	PIN_RC12,								//RC12 - Unused
	PIN_RC13,								//RC13 - Unused
	PIN_RC14,								//RC14 - Unused
	PIN_RC15,								//RC15 - Unused
	//PORTD
	PIN_RD0_HOB_HiA,						//RD0
	PIN_RD1_TERMINAL_TX,					//RD1
	PIN_RD2,								//RD2 - Unused
	PIN_RD3,								//RD3 - Unused
	PIN_RD4_LOB_HiA,						//RD4
	PIN_RD5_LOA_HiA,						//RD5
	PIN_RD6,								//RD6 - Unused
	PIN_RD7,								//RD7 - Unused
	PIN_RD8_HOA_HiA,						//RD8 - Unused
	PIN_RD9_GREEN_LED,						//RD9
	PIN_RD10_RED_LED,						//RD10
	PIN_RD11_BLUE_LED,						//RD11
	//PORTE
	PIN_RE0,								//RE0 - Unused
	PIN_RE1,								//RE1 - Unused
	PIN_RE2,								//RE2 - Unused
	PIN_RE3,								//RE3 - Unused
	PIN_RE4,								//RE4 - Unused
	PIN_RE5_SWITCHED_GROUND5,				//RE5
	PIN_RE6_SWITCHED_GROUND4,				//RE6
	PIN_RE7_SWITCHED_GROUND3,				//RE7
	//PORTF
	PIN_RF0,								//RF0 - Unused
	PIN_RF1,								//RF1 - Unused
	PIN_RF2_HOB_HiV,						//RF2 - Unused
	PIN_RF3_HOA_HiV,						//RF3 - Unused
	PIN_RF4_LOA_HiV,						//RF4
	PIN_RF5_LOB_HiV,						//RF5
	PIN_RF6,								//RF6 - Unused
	//PORTG
	PIN_RG2,								//RG2 - Unused
	PIN_RG3,								//RG3 - Unused
	PIN_RG6_SWITCHED_GROUND1,				//RG6
	PIN_RG7_SWITCHED_GROUND2,				//RG7
	PIN_RG8,								//RG8 - Unused
	PIN_RG9,								//RG9 - Unused
	NUMBER_OF_PINS
};

enum A2D_PIN_DEFINITIONS
{
	A2D_AN0_TRANSFORMER_PRIMARY_MINUS = 0,		//A0
	A2D_AN1_TRANSFORMER_PRIMARY_PLUS = 1,		//A1
	A2D_AN2_SOLAR_PLUS = 2,						//A2
	A2D_AN3_TEMP2 = 3,							//A3
	A2D_AN4_UNUSED = 4,							//A4, used as programming line
	A2D_AN5_UNUSED = 5,							//A5, used as programming line
	A2D_AN6_TEMP1 = 6,							//A6
	A2D_AN7_TEMP3 = 7,							//A7
	A2D_AN8_TEMP4 = 8,							//A8
	A2D_AN9_INPUT_CURRENT = 9,					//A9
	A2D_AN10_OUTPUT_CURRENT = 10,				//A10
	A2D_AN11_TEMP5 = 11,						//A11
	A2D_AN12_VDC_BUS_PLUS = 12,					//A12
	A2D_AN13_TRANSFORMER_SECONDARY_PLUS = 13,	//A13
	A2D_AN14_VOUT_PLUS = 14,					//A14
	A2D_AN15_VOUT_MINUS = 15,					//A15
	NUMBER_OF_A2D_PINS
};

//Libraries
//Pins Library
#define PINS_MAJOR	2
#define PINS_MINOR	0
#define PINS_PATCH	0

//Scheduler Library
#define SCHEDULER_MAJOR	0
#define SCHEDULER_MINOR	1
#define SCHEDULER_PATCH	0

//Function Prototype
void Configure_For_Afriji(void);
void Heart_Beat_Task(unsigned long time_mS);

#endif	/* CONFIG_H */

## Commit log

2017-03-12 Initial Commit
    Contains most of what is required.
    Known Issues:
    Input stage is not coded to generate Sine Wave
    Output stage is coded for Sine Wave, but not connected to the stage to
    work correctly
    [15VDC Powersupply.SchDoc, 3.3VDC Powersupply.SchDoc, 32-Pin 0.1 inch header.stp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]
2017-03-12 Merge of Mike's File structure with Craigs
    Merge of Mike's File structure with Craigs
    [33mm trace test.dwg, Block Diagram.dwg, Circuit Calcs.xlsx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]
2017-03-12 Tweaks
    Input inverter pins should now be setup correctly, back end code to
    drive them has not been.
    Bugfix, diagonal pairs are now appearing to be firing correctly
    [Microcontroller.SchDoc, Sine Wave Table.xlsx]
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2017-03-24 Updated .Gitignore
    Deleted defunked v0.1.3 hardware design (included several deprecated
    features)
    Included Mikes 180 degree sine wave table
    [180deg.csv, 32-Pin 0.1 inch header.stp, Battery - 9V.step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]
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2017-03-25 A2D should *mostly* work
    Sample and convert time is NOT setup (will fail to compile)
    Code otherwise compiles, but I have not tested to see if it works
    [A2D.c, Config.c, Config.h]
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2017-03-28 Doesn't work...
    ...but the framework is very close to what invision the final being
    [Sine Wave Table.xlsx]
2017-03-28 Code Fixed?
    I reverted back to 100kHz so I can inspect the transistions with greater
    ease, but I still recommend going to 100kHz to get greater resolution
    [Inverter.c]
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2017-03-30 Quick Save before pivot
    [Microcontroller.SchDoc]
2017-03-30 I'm done for the night
    [Sine Wave Table.xlsx]
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2017-04-01 Cleaner Waveform (only bottom FETs PWM)
    -Enforced transformer current circulation on top FETs during 0 and 180º
    crossover points
    -Waveform guide now starts at 0º instead of assuming zero crossing will
    take care of it
    -Max PWM duty cycle is 95%
    -Scheduler is now set to 25uS to avoid overrun in the event of all
    events firing. This is the bare minimum and subject to future code
    -Fixed bug where the triggering FETs were turning "off" at the beginning
    of the wavefore and back on at the end, instead of vice versa
    [Inverter.c, main.c]
2017-04-01 100kHz (Bottom FETs PWMing only)
    -100kHz operation
    -Added multiplier/divider capaabilities back into the circuit to allow
    DC manipulation
    -Refactored inverterLevel variable to read as inverterOnPeriod so that
    it is more descriptive of what it is doing
    [Sine Wave Table.xlsx]
2017-04-01 Working! - 100kHz (Mike's Waveform)
    -Mike's Waveform triggers all of the FETs instead of just the bottom
    ones
    -It allows for circulating currents during the off-cycles through on
    FETs instead of body diodes
    -This is a cooler running operation version of the previous one that
    Micah and I came up with and then kludge fixed the resulting heating
    issue with diodes
    -Max duty cycle is now 90%
    -I drew waveforms to help visualize what is happening in the code
    -Old waveform code was commented out so we could do a comparisson as
    needed
    -Period was correctly set to 100kHz this time
    [Inverter.c]
2017-04-07 No Shoot Through - 100kHz - Mike Waveform
    -Reversed the order of the the registers so the shorter period one was
    set first
    -Due to double buffering the code was setting one first and then the
    next cycle started when the second register was being set but didn't
    take effect until the next cycle (1 in a million problems happen 16
    times a second)
    -Wavey/hairy output from transformer with ~40Vpp at the peak with a
    period of 1-1.6 mS
    -Placing the bathroom fan on it did not run nicely and our waveform
    became undescribably distorted
    -I believe the code required HOB in Positive_Sine to be reversed as
    others
2017-04-07 See previous commit
    I missed this file
    [Inverter.c]
2017-04-07 Prevent shoot through on startup
    -The default settings on the PWM turned all of the FETs on during the
    first second before the inverter code took over. The current limiting of
    the power supply was saving the day
    -These setting were fixed so that they are fully off during this period
    [Inverter.c]
2017-04-07 Reordered for safe double buffering
    -Finished placing the shortest items in the buffer in the event that the
    period rolls over between assignments
    [Inverter.c]
2017-04-07 See previous commit
    Missed a line of code
    [Inverter.c]
2017-04-09 Removed Accidental Overlap, Tightened Deadband
    Still suffers from shoot through. I believe the Always On/Off PWM code
    is the culprit and is allowing shoot through.
    -Waveforms that transistion lower are given first chance at being set
    low, this avoids accidental overlap if the waveform transitions and
    locks in a double buffer setting for a cycle before self correcting
    -Deadband can be semi-safely reduced down to 1 cycle, I chose 2 cycles
    to be 100% sure of no overlap
    -I redid the table so that it took the new deadbands into account. as
    well as a minimum on time of 2 cycles (ensures it can get fully on)
    -Ensured the advancing code was consistent and allowed full scale
    adjustments
    -The size of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
    [Sine Wave Table.xlsx]
2017-04-13 Tweaked for ~60Hz operation
    Beautifully runs the bathroom fan, but not the fridge :(
    [Sine Wave Table.xlsx, Tests.xlsx]
2017-04-14 Mutually exclusive inverter code added
    UNTESTED but compiles, and Hi-I stage seems to be working
    -Add support for mutually exclusive inverters to be running
    simultaneously, each capable of running independent of each other
    -Code to decouple the two has not been added
    -This will likely further reduce the number of unique steps that each
    can realisticly make due to doing twice as much as before
    [Microcontroller.SchDoc]
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2017-04-15 Frequency Controllable
    Ramp up frequency from 20Hz to 60Hz
    -Each inverter stage is using it's own structure now for easier code
    maintenance
    -The number of steps has been optimized to 10. This allows the code to
    run less often so I can do more, but still maintains an acceptably good
    sine wave a2 20/60 Hz
    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
    [Sine Wave Table.xlsx, Tests.xlsx]
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2017-04-15 A2D no longer resets board
    The A2D code was dividing by zero because of uninitialized channel 4 and
    5 (if it somehow got passed 4)
    -Added intialization code for all channels, this will be modified when a
    channel is setup
    -Configured the code to trigger samples again
    -Removed the vestigal auto conversion variables and definitions
    NOTE: The sample time is still set at max and needs to be revisited
    [A2D.c]
2017-04-15 A2D readings fixed
    Skipping an item in the scan skips the A2D Buffer (unbeknownst to me). I
    was reading and recording correctly from AN0 to AN3, but after that
    everything was shifted by two registers.
    -A2D code is reading the shifted registers
    -Requires an interupt on the 16th sample/convert sequence instead of
    14th due to the aforementioned issue
    -The current sense amplifier pins were lifted pending a redesign, as
    such the reading will only return -1 until it is fixed
    -Switched Grounds are now an always low open-drain output
    -HOA/LOA/HOB/LOB HiV/HiA are now back in there proper locations (Port
    ordered) in the pin initialization
    -LED indicators are now used to show LOA on the HiV and HiA inv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
    [Microcontroller.SchDoc]
2017-04-15 Added SLR to Hi-Current measurement
    The measurement is very noisy and has many spikes due to circuit
    ringing. The largest deviation I measured was +15A from an average of
    2.4A.
    Box car averaging slowed the result down to unacceptable speeds by the
    time the averaging was having a noticeable effect.
    A rolling average was not considered.
    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
    [Tests.xlsx]
2017-04-16 Added SRL to LoV sensing
    Vsolar was mostly stable, but benefitted from a small amount of SLR.
    The negative terminal of the transformers primary side was noisy between
    the average voltage and 0V, so it benefitted.
    The positive terminal of the transformers primary side had voltage
    spikes between average and 0V, and nearly +40V above, so it benefitted
    drastically from it.
    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
    [Microcontroller.SchDoc, Tests.xlsx]
2017-04-16 Added SLR to HiV
    Hi-Voltage lines definitely benefitted from Slew Rate Limiting
    -Just like the low voltage functions, I created individual formating
    functions that each had a localized memory
    [Tests.xlsx]
2017-04-16 Added SLR to LoI
    It didn't need it, but at this point I did it to keep the code
    consistent
    [Tests.xlsx]
2017-04-17 Added Compile Defines to Enable/Disable Hi-V Inverter
    Defining DUAL_INVERTER in the config.h file will enable the code to run
    the high voltage inverter
    [Tests.xlsx]
2017-04-19 Rudimentary Voltage Control [Untested]
    Step and hold voltage control will inch towards the target and stop as
    long as it is within the deadband
    -Voltage control is done at each peak and is simple step-and-hold
    control with a 2.4VAC deadband
    -Step and hold multiplier is capped between 1 and 100
    -A2D scan trigger now only occurs at the peaks and is part of the Peaks
    function
    -Positive and Negative functions now precompute the circulating and
    conducting periods and apply caps on them to prevent them from getting
    too big or too small
    -THEY ARE NOT CURRENTLY CHECKED TO AVOID OVERUNNING EACH OTHER
    -New defaults: divider is 100, target delay is 416
    -Removed vestigial adder code
    -Due to limitations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
    [Tests.xlsx]
2017-04-20 Rudimentary Voltage Control [Tested]
    It can go from no voltage to full voltage in 664mS.
    -A2Ds are still messed up, I tabbed the ones I have identified for sure
    for easy identification
    -Slew rate on Hi-V sensing was increased to 500mV
    -Added compile switches for controlling the PWM pins related to the
    second inverter
    -Reorganized the A2D channel initialization functions to they were in
    channel order
    -The default target voltage to follow is now 170.0V (120Vrms)
    -I sample the VDC bus now for voltage following instead of the
    transformer secondary
    -Dead band is now a fixed 1.0V
    [Microcontroller.SchDoc]
2017-04-20 Stability Lost
    The code should be the same, but now it oscillates.
    I need to compare this version and the previous version to see what
    changed!
    [Inverter.c, main.c]
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2017-04-21 Will not rumble freezer
    We have voltage and frequency control, can run the bathroom fan, but
    can't get the freezer to rumble.
    -Starts at 10Hz (20Hz didn't work)
    -Runs for 0.1S at 20Hz before frequency ramp kicks in
    -Starts with the full multiplier (max power output)
    -Maximum multiplier is now a defined number magic number instead of
    being just an unnamed number used in a few calculations
    [Inverter.c, main.c]
2017-04-22 Enabled second inverter stage [UNTESTED]
    Reenabled second inverter
    -Frequency is now 20Hz
    -It runs at 20Hz for 1 second before stepping up to 60Hz in 0.1S
    increments over a 4S period
    -Disabled voltage control and A2D peak measurements for second stage
    [Tests.xlsx]
2017-04-26 [Untested] Added code switches to enable/disable inverters
    Using simple code switches entire inverters can be removed from the code
    without affecting anything now.
    -Code switches renamed and/or created as HiI_INVERTER_ENABLED and
    HiV_INVERTER_ENABLED
    -Added copies of code switches to single stage code, modeling off of
    existing dual stage code
    -Removed vestigial code/comments from config.h that covered LED PWMs
    (never implemented), a buzzer (leftover from early dev board that had
    one), and a UART Terminal definition (never implemented)
    -Reordered inverter code for simplicity, Trigger_A2D_Scan is common to
    both inverters, but I duplicated them with the intention of the
    functionality changing i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
    [Config.c, Config.h, Inverter.c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]
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2017-04-27 Code prepped
    The code is setup to remove the high current inverter from the system
    and only use the high voltage inverter.
    -High Voltage is now correctly setup ramp up frequency, while High
    current targets a fixed 60Hz and constant 120Vrms
    -Disabled high current inverter using code switch
    -Removed compile warning about A2D timing being wrong as it is now a
    documented feture request on GitHub
    -Enabled voltage measurements for the voltage tracking, but haven't
    finalized how it works
    [A2D.c, Config.h, Inverter.c]
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2017-05-05 [Untested] Fixed ADC consistently out of order
    It was interrupting after 16 samples of 14 channels, which meant it
    would sample all 14 channels, then the first two channels again to fill
    the memory space.
    The next time it would start sampling with the "next" channel which
    likely is not the 1st channel.
    -Added compiler definition to allow applying my fix to be optional. I
    opted for this as I don't have hardware to test with right now so I
    don't know if this actually fixed the issue
    [A2D.c]
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2017-05-05 Forgot to save the spreadsheet, oops
    [SineFunctionLookup.xlsx]
2017-05-18 Refactored comments and schematic layout
    Fixed spelling mistakes in comments
    Centered thermistor sensing circuits
    Moved power supply block closer to input voltage
    [Overview.SchDoc]
2017-05-26 Applied Code Symmetry between Pos/Neg Sine Wave
    Rearranged the order so that it matched the order of implementation. It
    was thought that this might affect the output and explain why the
    positive wave form was malformed and the negative was not.
    It didn't...
    [Inverter.c]
2017-05-28 DOESN'T COMPILE: Half-way created Voltage Control
    Added lots of hooks for external control
    Added the framework new voltage control algorithims
    [Config.h, Inverter.c]
2017-06-01 UNFINISHED More implementation of voltage control
    New voltage control
    -Most functionality was added, still missing the Update_PWM_Register()
    -Place holders for variables are in place (whatAmI)
    -Removed lots of old defunkt code that was used in the previous voltage
    control paradigm
    Added lots of new magic numbers
    -100%
    -900º
    -180º
    -270º
    -360º
    Included Sine lookup table
    -Moved code from header to a new *.c file
    -Capable of doing a sine conversion with a final resolution of three
    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
    [Config.h, Inverter.c]
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2017-06-08 A2D is fully certifiable
    A2D is now just like the Death Star: Fully Functional
    Fixes #17
    [A2D.c, Inverter.c]
2017-06-13 UNTESTED Bug Fixes
    Set default values, pending external controls setting them.
    Fixed casting bugs in Converter_Time_To_Angle,
    Calculate_Amplitude_Factor, Calculate_PWM_Duty_Percent functions
    Finished adding compile excludable inverters using preprocessing
    definitions
    Added divide by zero sentinel
    Calculate_Amplitude_Factor was receiving the wrong variable for 'a' and
    it has been corrected to be a local static variable instead.
    [Inverter.c, main.c]
2017-06-19 UNTESTED General Bugfix
    There is an address error that is only present on 15Hz, so I included a
    kludge to bypass that frequency so that we can continue to test with the
    pot.
    Included a sentinel to ensure the Frequency can never go to 0Hz (will
    cause a math error)
    Fixed a bug with the target output voltage being 10 times bigger than it
    should have been (maybe fixing output voltage waveforms?)
    Added a PWM upper limit that is 3x deadband to always allow for a
    circulating current
    Added a PWM lower limit that is 1x deadband to always allow for a
    conducting current
    onTime is checked for validity, not circ/cond current periods. The code
    to make one limit affect the other was going to be brutal, so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
    [Inverter.c]
2017-07-10 UNFINISHED Hardware only updates
    Started working on the next version of the hardware. Incorporating all
    of the nougaty goodness we have learned on the current version.
    Doubled up H-Bridge FETs to improve efficiency and decrease thermal load
    on H-Bridge FETs
    H-Bridge drivers now control one side instead of kitty corner (Reduces
    inductance/ringing on control lines)
    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
    [32-Pin 0.1 inch header.stp, Battery - 9V.step, Battery - AA.step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]
2017-07-13 UNFINISHED Hardware only updates
    Added by-pass caps to all analog inputs
    H-Bridge Drivers now have 44uF (2x 22uF) bootstrap capacitors
    Added a 5V buck SMPS to convert incoming voltage to provide a
    conditioned input for the 3.3V linear and 15V boost SMPS
    Added a 15V boost SMPS to convert 5VDC into the voltage required to
    power the H-Bridge drivers
    Fixed HVGND so that it references the rest of the circuit correctly
    Removed the DC- voltage rail sensor as it became circuit ground
    Added a 6th Temperature sensor as there was a free analog pin
    [15VDC 500mA Boost SMPS.SchDoc, 3.3VDC 250mA Linear PS.SchDoc, 5VDC 250mA Buck SMPS.SchDoc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]
2017-07-13 See previous commit
    Added two more ToDos
    [PV Refridgerator.PrjPCB]
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2017-07-22 Library Changeover Completed
    Changed over libraries completely
    Added the beginnings of emergency thermal shutdown
    [15VDC 500mA Boost SMPS.SchDoc, 3.3VDC 250mA Linear PS.SchDoc, 5VDC 250mA Buck SMPS.SchDoc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]
2017-08-25 Bulk Capacitance and Emergency Thermal Shutdown
    Added Emergency Thermal Shutdown so the unit will automatically shutdown
    at 70C and not turn on until it has cooled to 50C
    Added 15-30 mF of bulk capacitance on the input and 1-2 mF on the output
    after the full-wave rectifier
    Cleaned up some old unused files
    [Component Selection.xlsx, Design Models.xlsx, Emergency Thermal Shutdown.SchDoc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]
2017-10-12 Werks fer mee
    Hi-V inverter is disabled
    Hi-V inverter has shoot through
    Frequency on both inverters is now broken out to be compile changed
    [Config.c, Config.h, Inverter.c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]
2017-10-14 First stage works
    Debug terminal was causing massive main loop overruns which was causing shoot through and malformed waves.
    Renabled second stage inverter.
    Default target voltage of each inverter is now set during initialization inside the compile switches.
    The hertz calculation code was damaged and I had to rewrite the return statement.
    Output stage has not been tested. Input stage runs beautifully.
    [Inverter.c, main.c]
2017-10-14 Untested: Bug Fixes/Code Cleanup
    All single line if statements now have open/closing braces to prevent future bugs.
    Removed shadow frequencies as they were not being used...well mostly. They were being set but never looked at. This is a feature that will need to be reimplemented at some point.
    OCM modules initialization are now included in the compile switches.
    [Inverter.c]
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2017-10-14 Fixes to inverter initialization
    1) Commented out Micah and Mike global variables for f and V targets
    2) Fixed V and f initialization values
    [Inverter.c]
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2017-10-15 Datasheet request
    The sync source for OCM modules should be set last to ensure correct operation. Ours was being set 5th out of 9 modules.
    [Inverter.c]
2017-10-15 Fixed Shoot Through
    If we are too close to a PWM roll over point, then we hard wait for the timer to roll over so that all of the shadow registers are set before they go live. This prevents two distinct errors that would randomly occur.
    1) Only one of the registers gets set before going live while the second register needs to wait a full cycle before going live.
    2) Three or fewer OCM are set and go live before the remaining ones do the following cycle.
    [Inverter.c]
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2017-10-19 Revert "Fixed Shoot Through"
    This reverts commit f6b5a9508a92bcde38a36a150cd09777196b4b83.
    [Inverter.c]
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2017-10-21 Added reverse voltage protection to input power supply
    A single diode to protect them all
    [Powersupply.SchDoc]
2017-10-21 Revert "Revert "Fixed Shoot Through""
    This reverts commit 313390958b5609e3800cda9c2dc30f7aabb44959.
    [Inverter.c]
2019-01-16 Simplified thermal shutdown formulae
    Combined and reworked the formulae to be easier to use.
    Removed raw files from the repository.
    [Emergency Thermal Shutdown.SchDoc]
2019-01-23 Repository Restructuring
    Removed unnecessary repository info
    Moved locations of files/folders
    Renamed files/folders
    [15VDC 500mA Boost SMPS.SchDoc, 15VDC Powersupply.SchDoc, 3.3VDC 250mA Linear PS.SchDoc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]
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
